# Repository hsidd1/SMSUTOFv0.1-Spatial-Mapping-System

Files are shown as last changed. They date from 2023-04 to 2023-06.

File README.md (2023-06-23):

# Spatial-Mapping-System
**The SMSUTOFv0.1 is an embedded spatial measurement device I've created which uses a VL53L1X time-of-flight sensor to acquire information about the area around you and generates a 3D mapping of a scanned area.**

Check out the datasheet for this project: [SMSUTOFv01 Datasheet](SMSUTOFv01-datasheet.pdf)

## Demo

<div style="display:flex; justify-content:center;">
  <div style="text-align:center;">
    <div>Area scanned:</div>
    
  </div>
  <div style="text-align:center;">
    <div>Output plot:</div>
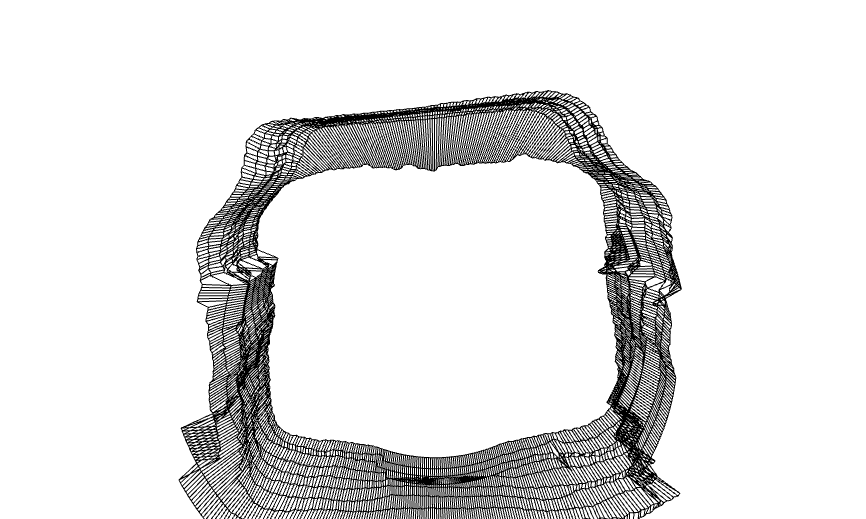
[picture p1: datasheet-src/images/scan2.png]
    
  </div>
</div>

## Setting up:

1. Build the circuit based on the following schematic:
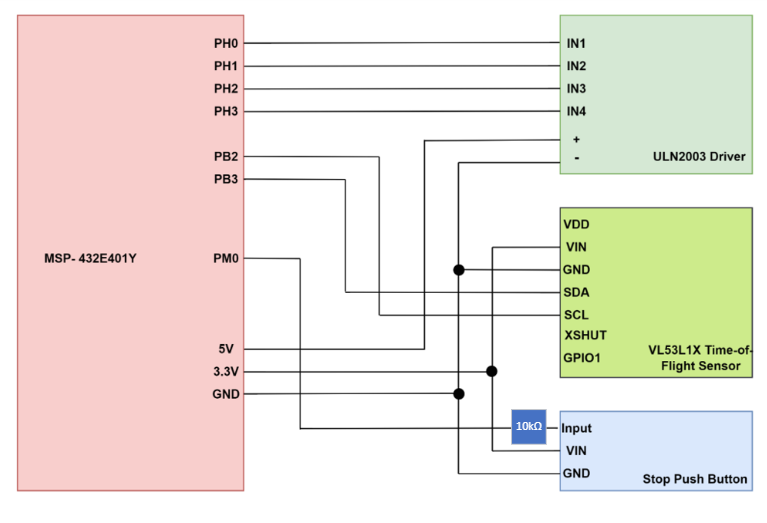
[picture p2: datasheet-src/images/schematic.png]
Circuit schematic


Ensure the ToF is mounted to the stepper motor. The Keil project should be flashed on the micro controller by default, so pressing the reset button is sufficient to load the program. If this is not the case: Open the Keil Project src found [here](main-keil) then translate, build and load the program.

## Software Installation:

The embedded C code can be run on [Keil uVision](https://www.keil.com/download/) and flashed directly onto the microcontroller from the IDE.

### Python Requirements

It is recommended to use a virtual environment, as this program uses libraries compatible upto [Python 3.9](https://www.python.org/downloads/). If you choose to do this with conda:

```sh
conda create -n <env-name> python=3.9
```

You can then install the required packages ([NumPy](https://numpy.org/doc/1.21/), [Open3D](http://www.open3d.org/docs/release/), and [Pyserial](https://pyserial.readthedocs.io/en/latest/pyserial.html)):

```sh
pip install -r requirements.txt
```

## How to use the device after setting up: 

1. Open `measurement_data.py` and modify the PORT variable to that of your device, found from UART port listed in device manager. 
2. Run `measurement_data.py` by opening terminal, navigating to the directory of the file, and entering `python measurement_data.py`
3. Enter how many displacement steps the scan will use when prompted by the program. 
4. Press the peripheral push button to enable measurements to set up the ToF. Pressing this again will toggle this back off.
5. Press the the onboard PJ1 button each time a measurement rotation has to be made. Pressing this again will end the rotation process.
6. For each number of physical steps taken, wait for the motor to complete one full rotation and return back to the home position. Once this is complete, move forward by the amount of x-displacement increment set (350 mm in the program but modifiable by user in the `STEP_INCREMENT` variable) 
7. Press the button again for the next measurement.
8. The program will then print to you the measurements at each point taken as the program runs from the scan and also output this to a file in the same directory called `pointdata.xyz`. D3 LED will flash on the micro controller for verification purposes. 
9. Run the `spatial_visualization.py` file by typing `python spatial_visualization.py` in terminal.
10. When prompted, enter the number of scans taken. The program will use this and then output the numerical value to the user in the console and output the visualization points on the screen in a GUI. Closing this screen will show a new screen with final spatial map in a GUI. 

The scan is of a yz-plane with x being the displacement taken for each scan. `y` and `z` are seen as the vertical plane that the motor rotates and scans for, and `x` is the displacement after physically moving the motor by the step increment defined.

The spatial map should now be visible to you in an interactive GUI window.

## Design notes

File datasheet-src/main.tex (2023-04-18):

\documentclass[12pt, letterpaper]{article}
\usepackage{graphicx}
\graphicspath{{images/}} 
\usepackage{titling}
\usepackage{amsmath}
\usepackage{listings}
\usepackage{xcolor}
\usepackage{textcomp}
\usepackage{multicol}
\usepackage[utf8]{inputenc}
\usepackage{parallel}
\usepackage{siunitx}
\usepackage{booktabs}
\usepackage{fancyhdr}
\usepackage{tabularx}
\usepackage{caption}
\usepackage[export]{adjustbox}
\usepackage[top=1in, left=0.5in, right=0.5in, bottom=1in]{geometry}
\addtolength{\topmargin}{0in}

\usepackage{libertine}
\renewcommand*\familydefault{\sfdefault}  %% Only if the base font of the document is to be sans serif
\usepackage[T1]{fontenc}

\title{Spatial Mapping System Using Time-of-Flight}
\author{Hamza Siddiqui - 400407170 - siddih38 }
\date{April 17, 2023}

%\begin{document}

\pagestyle{fancy}

\lhead{Hamza Siddiqui}
%\chead {\today}
\chead {April 17, 2023}
\rhead{SMSUTOF HS 2023 v0.1}

\onecolumn

\begin{figure}
\begin{minipage}{0.47\textwidth}
\centering
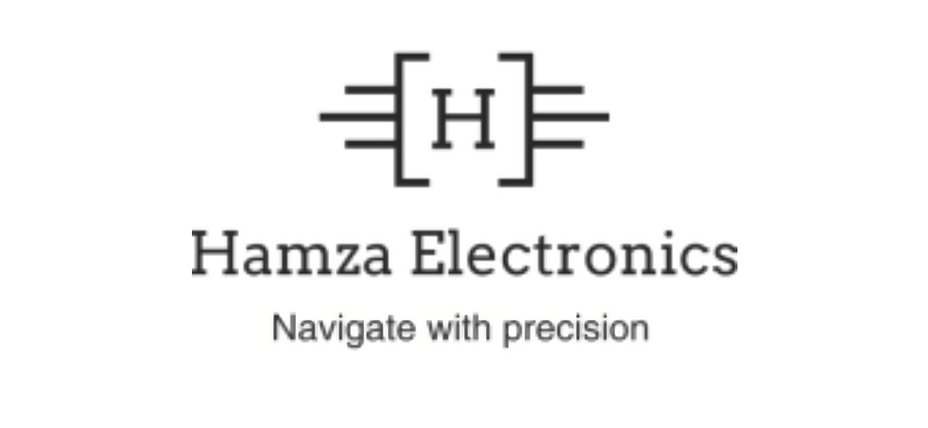
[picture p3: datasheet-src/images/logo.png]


\end{minipage}
\hfill
\begin{minipage}{0.47\textwidth}
\raggedleft
\Huge \textbf{Spatial Mapping System using ToF v0.1}
\end{minipage}
\end{figure}

\begin{figure}
\begin{minipage}{0.47\textwidth}

\section*{Core Device Components}
\begin{itemize}
    \item Microcontroller Unit (ARM\textregistered \ Cortex\textregistered-M4F TI MSP432E401Y SimpleLink\texttrademark) 
    \item Stepper Motor (28BYJ-48 Velleman\textregistered\ 5 VDC Stepper Motor with ULN2003 Driver Board)
    \item Time-of-Flight Sensor (ST FlightSense\texttrademark \ VL53L1X)
    \item Additional Push Button 
    \item Removable Sensor Mount (Hamza Electronics\texttrademark)
    \item Fiberboard Case (Hamza Electronics\texttrademark)
\end{itemize}

\end{minipage}
\hfill
\begin{minipage}{0.47\textwidth}
\centering
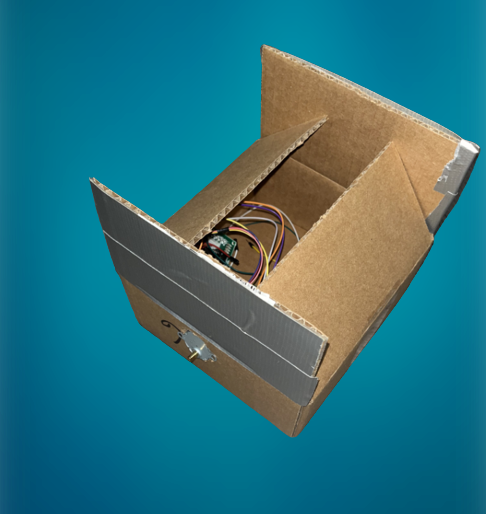
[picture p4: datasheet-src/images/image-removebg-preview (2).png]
 %PRODUCT IMAGE PLACEHOLDER

\end{minipage}
\end{figure}

\begin{document}
\maketitle
As a future member of the engineering profession, the student is responsible for performing the required work in an honest manner, without plagiarism and cheating.
Submitting this work with my name and student number is a statement and understanding that this work is my own and adheres to the Academic Integrity Policy of McMaster University and the Code of Conduct of the Professional Engineers of Ontario.
\thispagestyle{fancy}

\newpage
\section{Device Overview}
\subsection{Features}
\begin{multicols}{2}
\begin{itemize}
\item ARM Cortex-M4F TI MSP432E401Y Microcontroller (\$53.47)
    \begin{itemize}
        \item Bus frequency of 20MHz (configured via phase-locked loop; default core frequency of 120MHz)
        \item Four onboard LEDs - D3 flash functionality on each measurement
        \item Two onboard buttons (PJ1 for start/stop of motor rotation) and one reset button
        \item 1MB of flash, 256kB of SRAM
        \item  Communication interfaces including USB-OTG, CAN, Quad-SPI (QSSI), $\mathrm{I^2C}$, SPI,  and UART
        \item Two 12-Bit SAR-Based ADC Modules (2 Msps)
    \end{itemize}
\item MOT-28BYJ-48 Stepper Motor with ULN2003 driver (\$6.99)
    \begin{itemize}
        \item 5-12 VDC Operating Range 
        \item 64 steps/revolution 
        \item Frequency of 100Hz
        \item 4 phases with 4 step-indicator LEDs
    \end{itemize}
\item VL53L1X Time-of-Flight Sensor (\$25.32)
    \begin{itemize}
        \item Communication via $\mathrm{I^2C}$ (upto 400kHz)
        \item 4 m ranging and ranging frequency of 50Hz
        \item 2.6-5.5V supply range, 2.8V operating range
        \item Emitter: 940 nm invisible laser (Class1)
    \end{itemize}
\item Additional Push Button (\$0.60)
    \begin{itemize}
        \item Start/stop functionality for data acquisition
    \end{itemize}
\item Additional System Features
    \begin{itemize}
        \item UART serial communication between device and PC
        \item $\mathrm{I^2C}$ serial communication between device and Time-of-Flight sensor
        \item Baud rate of 115200
        \item C-language programming for device instructions, Python programming for visualization (via Pyserial and Open3d)
    \end{itemize}
\end{itemize}
\end{multicols}
\subsection{General Description}
To begin data acquisition, the additional push button is pressed to enable data processing, then the onboard button is pressed to begin taking measurements by spinning the motor and interfacing with the Time-of-Flight (ToF) sensor. The SMSUTOF HS 2023 utilizes a transducer which provides a digital output. Spatial distance measurements are acquired via the ToF sensor using $\mathrm{I^2C}$, while displacement is fixed at 30 cm. At each angle a measurement is taken, the D3 LED flashes. Together these measurements allow the device to measure a 3-D area. These signals are converted to electric signals, then conditioned into digital form and are finally converted to discrete digital values during the ADC process. The system communicates this to the user PC via UART asynchronous serial communication. A Python program is run on the PC and interfaces via their UART COM port and a baud rate of 115200, which then transfers measurement data to the PC and allows it to be stored in a .xyz file. This collected data is then used to generate a 3-D plot of the area that has been scanned via a Python program using open3d. The points for this plot are generated using trigonometric properties based on the angle and y,z coordinates generated, along with the fixed x-coordinate increment. If at anytime the button is pressed again during the scanning process, the data acquisition will be stopped. 
\subsection{Block Diagram (Data Flow Graph)}
\begin{figure}[h]
    \centering
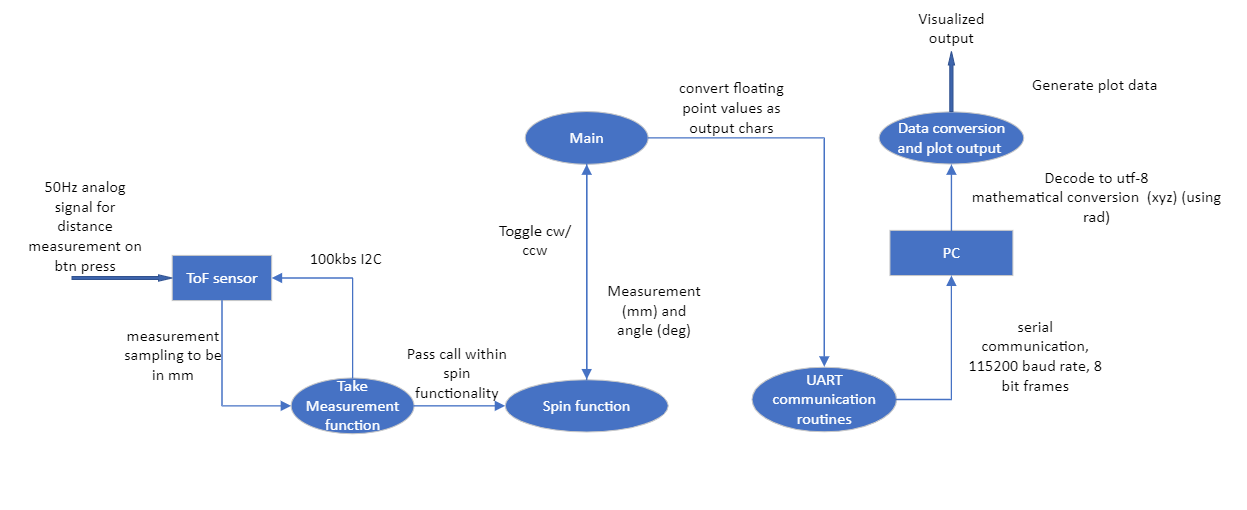
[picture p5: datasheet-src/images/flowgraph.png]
    
    \caption{Flow graph}
    \label{fig:flowgraph}
\end{figure}

\section{Device Characteristics Table}
\begin{center}
\begin{tabularx}{0.5\textwidth}{|>{\centering\arraybackslash}X|>{\centering\arraybackslash}X|>{\centering\arraybackslash}X|}
\hline
\textbf{Characteristic} & \textbf{Description} \\
\hline
Bus Speed & 20MHz \\
\hline
Serial Port & COM4 \\
\hline
Communication Speed & 115200 bps \\
\hline
Measurement Status & D3 \\
\hline
\end{tabularx}
\captionof{table}{Device Characteristics}
\end{center}

\begin{minipage}{0.48\textwidth}
\centering
\textbf{Stepper Motor Pin Assignments}
\begin{tabular}{|c|c|}
\hline
\textbf{ULN2003 Driver Board} & \textbf{MCU} \\
\hline
+ (5V) & 5V \\
\hline
- (5V) & GND \\
\hline
IN1 & PH0 \\
\hline
IN2 & PH1 \\
\hline
IN3 & PH2 \\
\hline
IN4 & PH3 \\
\hline
\end{tabular}
\captionof{table}{Stepper Motor Pinout}
\end{minipage}
\hfill
\begin{minipage}{0.48\textwidth}
\centering
\textbf{Time-of-Flight Sensor Pin Assignments}
\begin{tabular}{|c|c|}
\hline
\textbf{VL53L1X} & \textbf{MCU} \\
\hline
VDD & - \\
\hline
VIN & VCC (3.3V or 5V) \\
\hline
GND & GND \\
\hline
SDA & PB3 (I2C0 SDA) \\
\hline
SCL & PB2 (I2C0 SCL)  \\
\hline
XSHUT & - \\
\hline
GPIO1 & - \\
\hline
\end{tabular}
\captionof{table}{Time-of-Flight Sensor Pinout}
\end{minipage}

\section{Detailed Description}
\subsection{Distance Measurement}\label{Distance Measurement}
\textbf{Acquisition:}\\
The VL53L1X sensor utilizes Light Detection and Ranging (LIDAR) technology to accurately measure distances. It emits a pulse of light with a wavelength of 940 nm, which is then reflected back to the sensor by an object (maximum 4 m away). The sensor measures the time it takes for the emitted light pulse to reach the object and be reflected back to the detector. By utilizing the known speed of light and the measured time, the VL53L1X calculates the distance to the object with high accuracy as follows:
$$Measured\ Distance = \frac{Photon\ Travel\ Time}{2}\times Speed\ of\ Light$$ The sensor is mounted to a motor that completes 360 degree rotations (512 steps). At every 64 steps, or 45 degrees, a user LED is flashed to indicate a measurement (in mm) has been taken by the sensor. This is achieved through interfacing with the sensor and micro controller via $\mathrm{I^2C}$ serial communication. In total, this allows for 8 measurements to be taken in a single rotation, and the program can be modified to measure at smaller number of steps to take more measurements for more accuracy at the cost of time (use-case dependent configuration). \\ 
\textbf{Data Processing:} \\
Data is processed and converted via mathematical computation. When given the motor's angle $\theta$, the program increments by the measurement angle rotation each time and computes the coordinates using trigonometric properties. This is computed as $angle = steps/(TOTAL STEPS) \times 2\pi$ where steps is incremented by 45 degrees and TOTAL STEPS is set to 512 - these reset each time a rotation is complete i.e. when 512 steps have completed. For a given distance measurement $r$, we obtain that $y = r\cos{\theta}$ and $z = r\sin{\theta}$ for the vertical plane. X coordinate is computed through configuring a physical step increment taken for each successive measurement rotation in the program and incrementing the coordinate for the next spatial scan based on this value (350mm default configuration). This is the displacement for each scan. Together these coordinates can be used for plotting and mapping. \\
\textbf{Example Calculation:} 
\begin{figure}[h]
    \centering
    \begin{minipage}{0.5\textwidth}
        Suppose a measurement $r$ is measured as 3 m at an angle of 45 degrees. Then,
        \begin{align*}
            y &= r\cos{45}\\
              &= 3\cos{45}\\
              &= 2.12132034356 \ \text{m}
        \end{align*}
        and 
        \begin{align*}
            z &= r\sin{45}\\
              &= 3\sin{45}\\
              &= 2.12132034356 \ \text{m}
        \end{align*}
    \end{minipage}%
    \begin{minipage}{0.5\textwidth}
        \centering
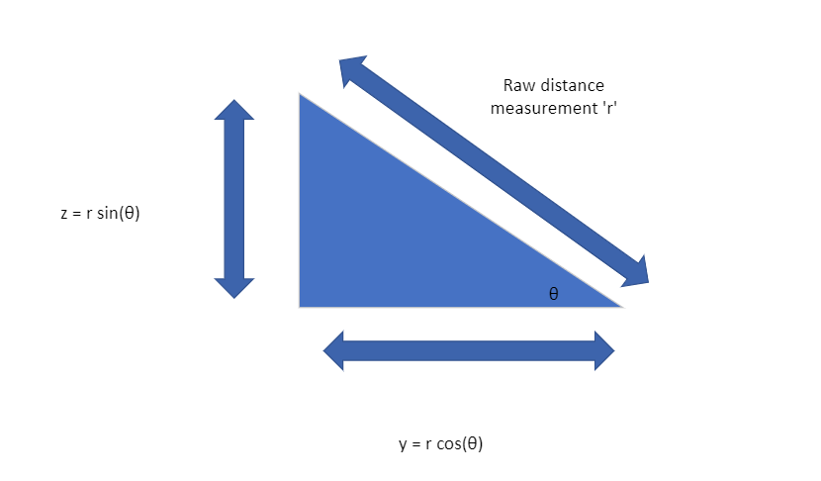
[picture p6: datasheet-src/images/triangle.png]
        
    \end{minipage}
    \caption{Trigonometric Conversion: Solving for $y$ and $z$ using the sine and cosine functions.}
    \label{fig:trig_conversion}
\end{figure}

\subsection{Visualization}
The visualization is achieved through Python using the NumPy, open3d, and PySerial libraries. Data is communicated using UART and a specified PORT which is accessed via PySerial. The measurement data from the micro controller is then communicated to the PC and is processed as points following the previously outlined conversion method. The points are then written to a .xyz file in the format of "x y z" per line, and is outputted on the console in the same manner for the user to view measurements printed in real time for each measurement. Next, using open3d, the points are viewed numerically by conversion using NumPy. 
\\Here is an example of how to read a point cloud using the Open3D library:

{\fontsize{10pt}{12pt}\selectfont % set font size to 10pt with 12pt line spacing
    \ttfamily % switch to monospaced font
    \begin{verbatim}
        pcd = o3d.io.read_point_cloud("pointdata.xyz", format="xyz")

    \end{verbatim}
}
In this code snippet, the variable \verb|pcd| stores the point cloud data read from the file \verb|pointdata.xyz|. The \verb|format| parameter specifies the format of the file, which in this case is XYZ format. 
These are then visualized using the following function call:
{\fontsize{10pt}{12pt}\selectfont % set font size to 10pt with 12pt line spacing
    \ttfamily % switch to monospaced font
    \begin{verbatim}
    o3d.visualization.draw_geometries([pcd])
    \end{verbatim}
}
Next, each vertex from the data is appended and the coordinates to connect lines in each yz slice is defined. The lines are then mapped to the 3D coordinate vertices as a line set and are then outputted to the GUI for visualization with the following function calls:
{\fontsize{10pt}{12pt}\selectfont % set font size to 10pt with 12pt line spacing
    \ttfamily % switch to monospaced font
    \begin{verbatim}
    line_set = o3d.geometry.LineSet(
        points=o3d.utility.Vector3dVector(np.asarray(pcd.points)),
        lines=o3d.utility.Vector2iVector(lines)
    )

    o3d.visualization.draw_geometries([line_set])
    \end{verbatim}
}

In this code snippet, the \verb|LineSet| class is used to create a line set from a set of points and lines. The \verb|points| argument is a vector of 3D points, and the \verb|lines| argument is a vector of pairs of point indices that define the line segments. The resulting line set is then visualized using the \verb|draw_geometries| function from the Open3D visualization module.

\section{Application Example with Expected Output}

A spatial scan can be taken of a room with a set number of displacement increments. An example room with an expected output can be seen below:

\begin{figure}[htbp]
\centering
\begin{minipage}{0.48\textwidth}
\centering

\subcaption{Hallway POV 1}
\label{fig:hallway1}
\end{minipage}
\hfill
\begin{minipage}{0.48\textwidth}
\centering

\subcaption{Hallway POV 2}
\label{fig:hallway2}
\end{minipage}
\caption{Hallway scanned}
\label{fig:hallways}
\end{figure}

\begin{figure}[htbp]
\centering
\fbox{\begin{minipage}{0.48\textwidth}
\centering
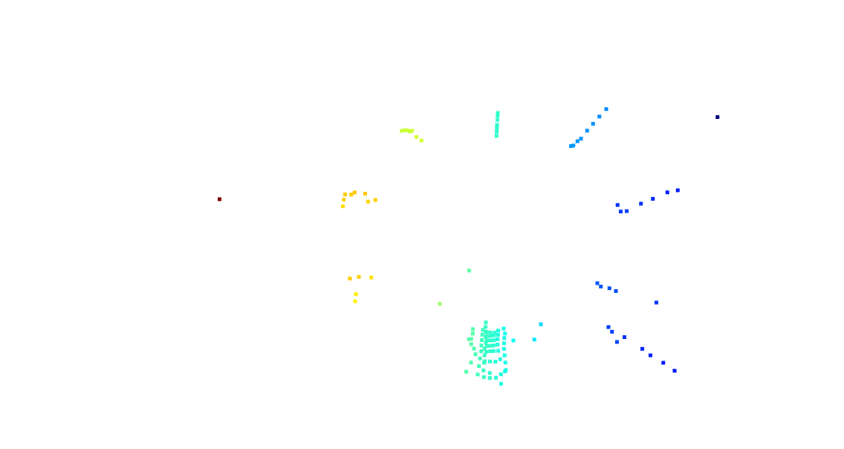
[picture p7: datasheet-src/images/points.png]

\subcaption{Point Visualization}
\label{fig:points}
\end{minipage}}
\hfill
\fbox{\begin{minipage}{0.48\textwidth}
\centering
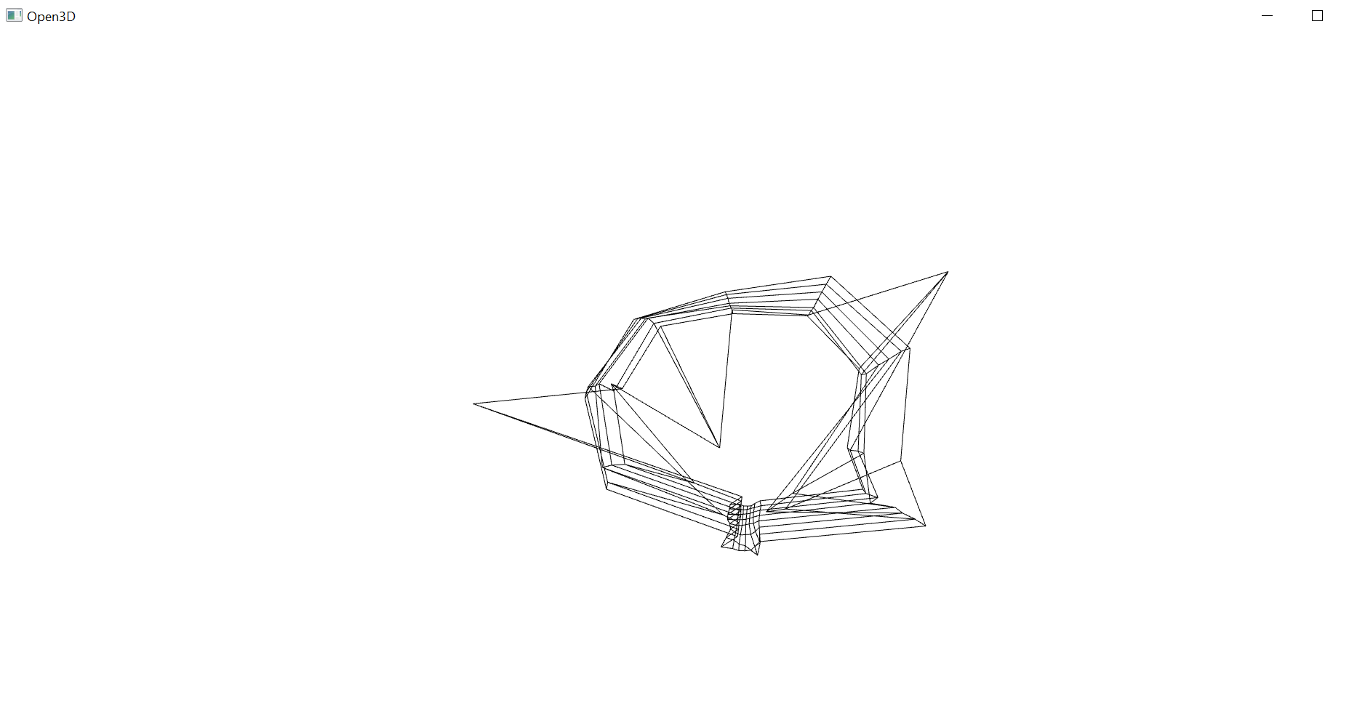
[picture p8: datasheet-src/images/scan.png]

\subcaption{Final output spatial map}
\label{fig:scan}
\end{minipage}}
\caption{Expected output of scan}
\label{fig:scan}
\end{figure}
 \newpage
\section{User's Guide}
Setting up: \\
Build the circuit based on the schematic provided in section \ref{sec:Circuit Schematic}. Ensure the ToF is mounted to the stepper motor. The Keil project should be flashed on the micro controller by default, so pressing the reset button is sufficient to load the program. If this is not the case: Open the Keil Project src from the provided code and $Translate$ \rightarrow build \rightarrow load. \\

Software Installation:
\begin{enumerate}
    \item Download Python 3.9, which can be found at https://www.python.org/downloads/ under specific release downloads.
    \item Install NumPy, open3d, and Pyserial by opening terminal and typing:
\begin{verbatim}
pip install numpy
pip install open3d
pip install pyserial
\end{verbatim}
Refer to their documentation for any issues:
\begin{itemize}
\item NumPy documentation: \url{https://numpy.org/doc/1.21/}
\item Open3D documentation: \url{http://www.open3d.org/docs/release/}
\item Pyserial documentation: \url{https://pyserial.readthedocs.io/en/latest/pyserial.html}
\end{itemize}
\end{enumerate}

How to use the device after setting up: 
\begin{enumerate}
    \item Open \verb|measurement_data.py| and modify the PORT variable to that of your device, found from UART port listed in device manager. 
    \item Run \verb|measurement_data.py| by opening terminal, navigating to the directory of the file, and entering \verb|python measurement_data.py|
    \item Enter how many displacement steps the scan will use when prompted by the program. 
    \item Press the peripheral push button to enable measurements to set up the ToF. Pressing this again will toggle this back off.
    \item Press the the onboard PJ1 button each time a measurement rotation has to be made. Pressing this again will end the rotation process.
    \item For each number of physical steps taken, wait for the motor to complete one full rotation and return back to the home position. Once this is complete, move forward by the amount of x-displacement increment set (350 mm in the program but modifiable by user in the \verb|STEP_INCREMENT| variable) 
    \item Press the button again for the next measurement.
    \item The program will then print to you the measurements at each point taken as the program runs from the scan and also output this to a file in the same directory called \verb|pointdata.xyz|. D3 LED will flash on the micro controller for verification purposes. 
    \item Run the \verb|spatial_visualization.py| file by typing \verb|python spatial_visualization.py| in terminal.
    \item When prompted, enter the number of scans taken. The program will use this and then output the numerical value to the user in the console and output the visualization points on the screen in a GUI. Closing this screen will show a new screen with final spatial map in a GUI. 
\end{enumerate}
As explained earlier, the scan is of a yz plane with x being the displacement taken for each scan. y and z are seen as the vertical plane that the motor rotates and scans for, and x is the displacement after physically moving the motor by the step increment defined. Refer to section \ref{Distance Measurement} for more detailed information with example calculations.

\section{Limitations}
\begin{itemize}
    \item \textbf{FLoating Point Capability: }The micro controllers features a 120-MHz Arm® Cortex®-M4F Processor Core With Floating Point Unit (FPU). The FPU fully supports various single-precision operations such as add, subtract, multiply, divide, multiply-and-accumulate, and square root. It also provides conversions between fixed-point and floating-point data formats, and floating-point constant instructions. It has 32 dedicated 32-bit single-precision registers, which are also addressable as 16 double-word registers. With the limitation of bits, the computations communicated to the PC are given with truncation. The trigonometric computations done by Python's math library add to this as the infinite series are accurate to limits of double-precision floating-point arithmetic, 15 to 17 decimal digits. Together the accumulation of these truncations result in an imperfect calculation of points, however minimal. Furthermore the trignometric functions assume fixed angle inputs, which may be subject to error by upto a few degrees, hence the point is not computed at the exact angle the sensor was oriented at. This allows for the points to still be accurate to a certain reasonable precision without being entirely perfect. 
    \item \textbf{ToF Quantization Error: } The ToF module includes a quantization error in the ADC process. Quantization error is the difference between the analog signal and the closest available digital value at each sampling instant from the A/D converter. It is equivalent to resolution. It is computed using $m = 8$ from  the ADC module bits and $V_{FS} = 3.3\ \text{V}$.
    \begin{align*}
        resolution &= \frac{V_{FS}}{2^m} \\
                   &= \frac{3.3}{2^8} \\
                   &= 0.0129\ \text{V}
    \end{align*}
    \item \textbf{Serial Communication: } The maximum serial communication rate of the PC can be found from device manager and is seen as 128000 bps as seen in the UART port. The rate is limited when using the micro controller as the rate is capped at a baud rate of 115200 bps. This can be verified by interfacing with UART at different baud rates until receiving an error. An example can be seen below: 

\begin{figure}[htbp]
\centering
\begin{minipage}{0.48\textwidth}
\centering
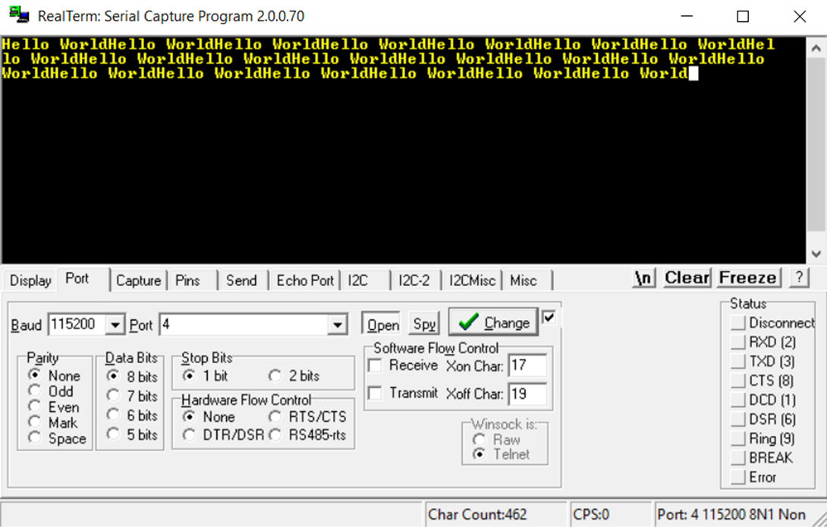
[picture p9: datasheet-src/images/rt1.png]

\subcaption{RealTerm output at 115200 baud rate}
\label{fig:rt1}
\end{minipage}
\hfill
\begin{minipage}{0.48\textwidth}
\centering
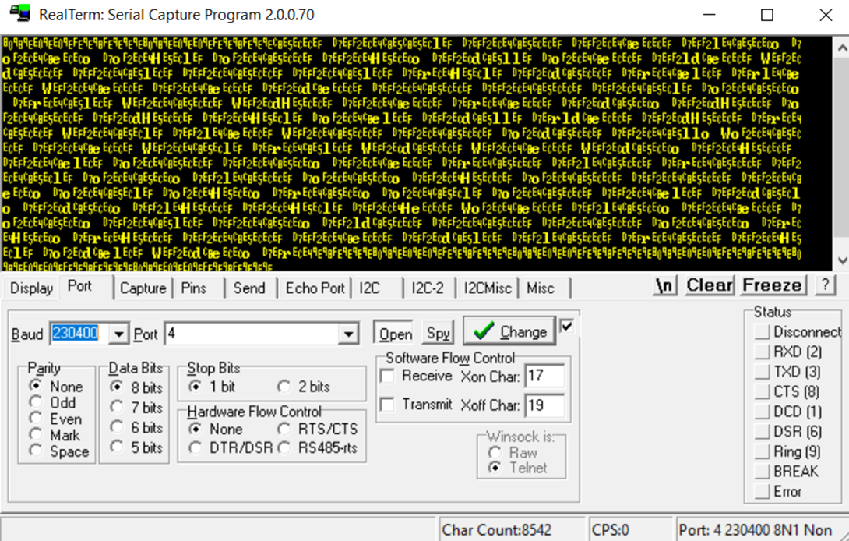
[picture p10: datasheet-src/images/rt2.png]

\subcaption{RealTerm output above 115200 bps}
\label{fig:rt2}
\end{minipage}
\caption{Verification of maximum standard serial communication rate}
\label{fig:rt_verification}
\end{figure}
The microcontroller and time-of-flight modules communicate via I2C serial communication. The I2C ports on the microcontroller are configured with a 100 kbps clock (in standard mode), as specified in the datasheet. In this setup, the microcontroller assumes the role of leader while the time-of-flight sensor acts as the follower and operates based on the microcontroller's clock speed. 

\item \textbf{Speed Limitations: } The speed of the stepper motor is accounted for with 512 steps and delays using \verb|SystickWait(4000)| with a 20MHz bus speed. This gives a motor speed of 0.4096 s per rotation without measurement delays between. 
The ToF also had a speed limitation with a very quick default speed from the overall calculation formula mentioned, however the delays within the program outweigh this speed and become the limitation. The delay called was of 50ms. This was verified by toggling a GPIO output port before and after spinning, and before and after measuring, then visualizing this using oscilloscope probes from an Analog Discovery 2 board with a generated waveform, and visualizing the pulse generated for each. 
\end{itemize} 
\\
\section{Circuit Schematic}\label{sec:Circuit Schematic}

Below is the circuit schematic for the device:

\begin{figure}[htbp]
\centering

\caption{Circuit Schematic}
\end{figure}
\newpage
\section{Programming Logic Flowchart(s)}
Below is the programming logic flowchart of the system:
\begin{figure}[htbp]
\centering
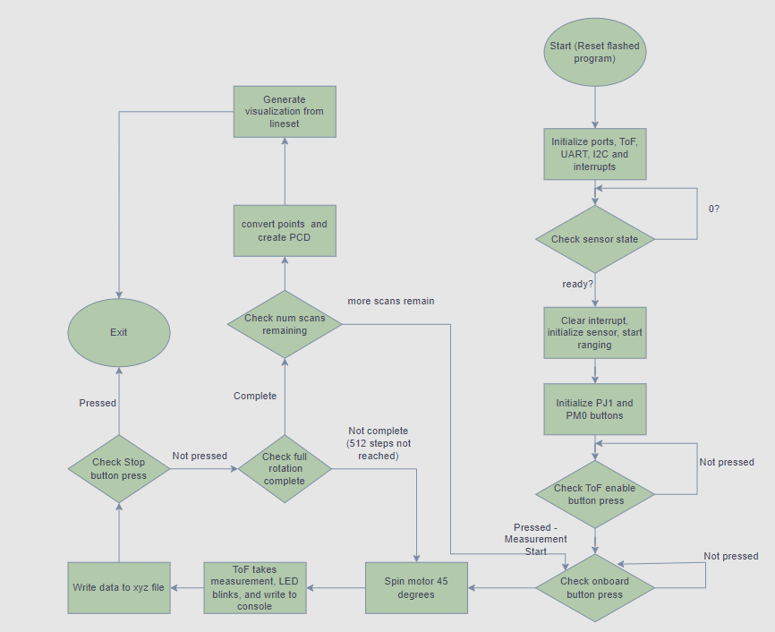
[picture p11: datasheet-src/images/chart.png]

\caption{Logic Flowchart}
\end{figure}
\newpage
\section{Additional Diagrams}
\begin{figure}[htbp]
\centering
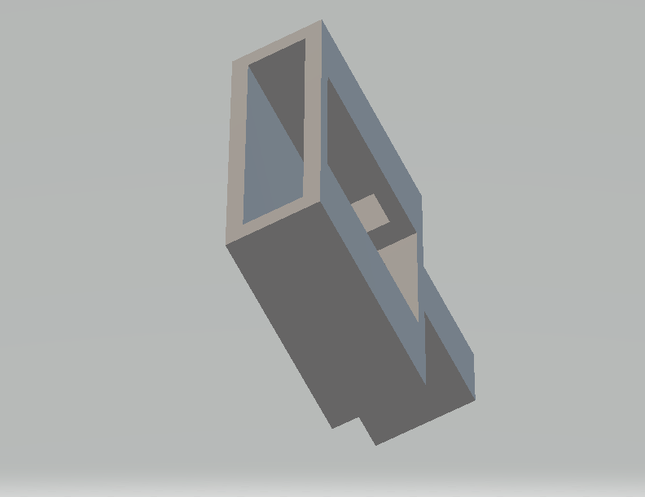
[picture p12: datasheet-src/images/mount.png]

\caption{ToF Mount STL}
\end{figure}
\end{document}

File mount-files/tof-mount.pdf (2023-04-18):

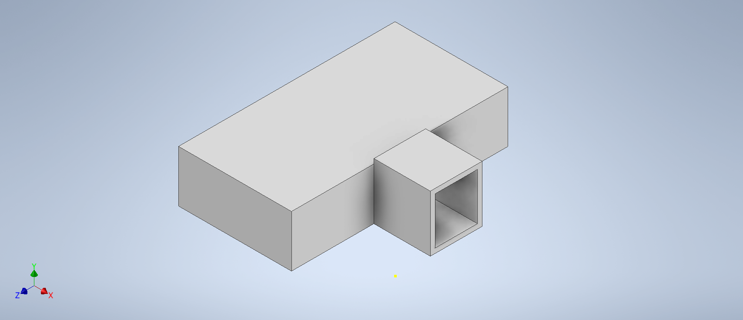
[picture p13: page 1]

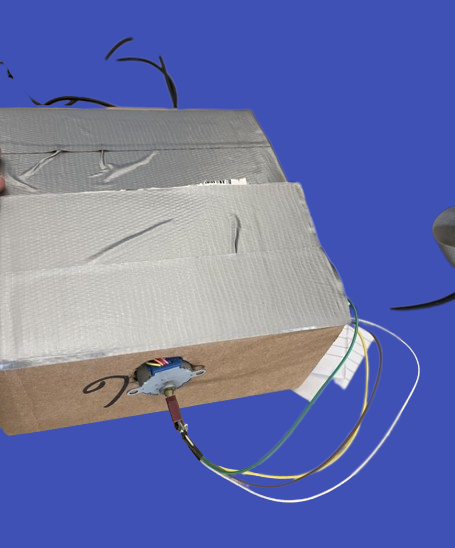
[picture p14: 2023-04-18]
datasheet-src/images/product.png

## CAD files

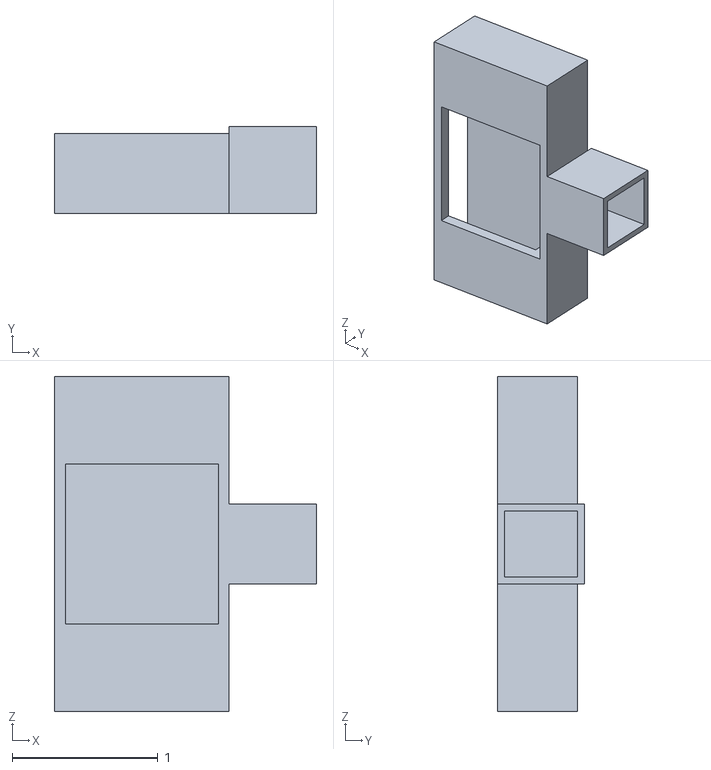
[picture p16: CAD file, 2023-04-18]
mount-files/tof-mount.stl
1.80 x 0.6 x 2.30

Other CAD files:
mount-files/tof-mount.ipt

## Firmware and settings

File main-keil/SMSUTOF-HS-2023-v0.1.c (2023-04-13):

#include <stdint.h>
#include "PLL.h"
#include "SysTick.h"
#include "uart.h"
#include "onboardLEDs.h"
#include "tm4c1294ncpdt.h"
#include "VL53L1X_api.h"
//#include "math.h"

// I2C configuration        
#define I2C_MCS_ACK             0x00000008  // Data Acknowledge Enable
#define I2C_MCS_DATACK          0x00000008  // Acknowledge Data
#define I2C_MCS_ADRACK          0x00000004  // Acknowledge Address
#define I2C_MCS_STOP            0x00000004  // Generate STOP
#define I2C_MCS_START           0x00000002  // Generate START
#define I2C_MCS_ERROR           0x00000002  // Error
#define I2C_MCS_RUN             0x00000001  // I2C Master Enable
#define I2C_MCS_BUSY            0x00000001  // I2C Busy
#define I2C_MCR_MFE             0x00000010  // I2C Master Function Enable

#define MAXRETRIES              5           // number of receive attempts before giving up

// initialising ports, protocols, etc
void I2C_Init(void){
  SYSCTL_RCGCI2C_R |= SYSCTL_RCGCI2C_R0;           													// activate I2C0
  SYSCTL_RCGCGPIO_R |= SYSCTL_RCGCGPIO_R1;          												// activate port B
  while((SYSCTL_PRGPIO_R&0x0002) == 0){};																		// ready?
    GPIO_PORTB_AFSEL_R |= 0x0C;           																	// 3) enable alt funct on PB2,3       0b00001100
    GPIO_PORTB_ODR_R |= 0x08;             																	// 4) enable open drain on PB3 only
    GPIO_PORTB_DEN_R |= 0x0C;             																	// 5) enable digital I/O on PB2,3
//    GPIO_PORTB_AMSEL_R &= ~0x0C;          																// 7) disable analog functionality on PB2,3
                                                                            // 6) configure PB2,3 as I2C
//  GPIO_PORTB_PCTL_R = (GPIO_PORTB_PCTL_R&0xFFFF00FF)+0x00003300;
  GPIO_PORTB_PCTL_R = (GPIO_PORTB_PCTL_R&0xFFFF00FF)+0x00002200;    //TED
    I2C0_MCR_R = I2C_MCR_MFE;                      													// 9) master function enable
    I2C0_MTPR_R = 0b0000000000000101000000000111011;                       	// 8) configure for 100 kbps clock (added 8 clocks of glitch suppression ~50ns)
//    I2C0_MTPR_R = 0x3B;                                        						// 8) configure for 100 kbps clock
}

//The VL53L1X needs to be reset using XSHUT.  We will use PG0
void PortG_Init(void){
    //Use PortG0
    SYSCTL_RCGCGPIO_R |= SYSCTL_RCGCGPIO_R6;                // activate clock for Port N
    while((SYSCTL_PRGPIO_R&SYSCTL_PRGPIO_R6) == 0){};    // allow time for clock to stabilize
    GPIO_PORTG_DIR_R &= 0x00;                                        // make PG0 in (HiZ)
  GPIO_PORTG_AFSEL_R &= ~0x01;                                     // disable alt funct on PG0
  GPIO_PORTG_DEN_R |= 0x01;                                        // enable digital I/O on PG0
                                                                                                    // configure PG0 as GPIO
  //GPIO_PORTN_PCTL_R = (GPIO_PORTN_PCTL_R&0xFFFFFF00)+0x00000000;
  GPIO_PORTG_AMSEL_R &= ~0x01;                                     // disable analog functionality on PN0

    return;
}

//XSHUT     This pin is an active-low shutdown input; 
//					the board pulls it up to VDD to enable the sensor by default. 
//					Driving this pin low puts the sensor into hardware standby. This input is not level-shifted.
void VL53L1X_XSHUT(void){
    GPIO_PORTG_DIR_R |= 0x01;                                        // make PG0 out
    GPIO_PORTG_DATA_R &= 0b11111110;                                 //PG0 = 0
    FlashAllLEDs();
    SysTick_Wait10ms(10);
    GPIO_PORTG_DIR_R &= ~0x01;                                            // make PG0 input (HiZ)
    
}

// Initializing port H for stepper motor 
void PortH_Init(void){
    //Use PortM pins for output
    SYSCTL_RCGCGPIO_R |= SYSCTL_RCGCGPIO_R7;                // activate clock for Port N
    while((SYSCTL_PRGPIO_R&SYSCTL_PRGPIO_R7) == 0){};   // allow time for clock to stabilize
    GPIO_PORTH_DIR_R |= 0xFF;                                       // make PN0 out (PN0 built-in LED1)
  GPIO_PORTH_AFSEL_R &= ~0xFF;                                  // disable alt funct on PN0
  GPIO_PORTH_DEN_R |= 0xFF;                                     // enable digital I/O on PN0
                                                                                                    // configure PN1 as GPIO
  //GPIO_PORTM_PCTL_R = (GPIO_PORTM_PCTL_R&0xFFFFFF0F)+0x00000000;
  GPIO_PORTH_AMSEL_R &= ~0xFF;                                  // disable analog functionality on PN0      
    return;
}

// Initialising for configuring ports for onboard assigned LED
void PortF0F4_Init(void) { // F4 - measurement status, F0 - Additional status
    SYSCTL_RCGCGPIO_R |= SYSCTL_RCGCGPIO_R5; //activate the clock for Port F
    while ((SYSCTL_PRGPIO_R & SYSCTL_PRGPIO_R5) == 0) {};//allow time for clock to stabilize
    GPIO_PORTF_DIR_R = 0b00010001; //Make PF0 and PF4 outputs, to turn on LED's
    GPIO_PORTF_DEN_R = 0b00010001;
    return;
}

// Initiasiling Port M for buttons - start/stop spinning and start/stop recording
void PortM0M1M2M3_Init(void) {
    SYSCTL_RCGCGPIO_R |= SYSCTL_RCGCGPIO_R11; //activate the clock for Port M
    while ((SYSCTL_PRGPIO_R & SYSCTL_PRGPIO_R11) == 0) {}; //allow time for clock to stabilize
    GPIO_PORTM_DIR_R = 0b00000000; // Make PM0:PM3 inputs, reading if the button is pressed or not
    GPIO_PORTM_DEN_R = 0b00001111; // Enable PM0:PM3
    return;
}

// Give clock to Port J and initalize as input GPIO-- 0 and 1 for now 
void PortJ_Init(void){
	SYSCTL_RCGCGPIO_R |= SYSCTL_RCGCGPIO_R8;					// Activate clock for Port J
	while((SYSCTL_PRGPIO_R&SYSCTL_PRGPIO_R8) == 0){};	// Allow time for clock to stabilize
  GPIO_PORTJ_DIR_R &= ~0x03;    										// Make PJ1 input 
  GPIO_PORTJ_DEN_R |= 0x03;     										// Enable digital I/O on PJ1
	
	GPIO_PORTJ_PCTL_R &= ~0x000000FF;	 								//? Configure PJ1 as GPIO 
	GPIO_PORTJ_AMSEL_R &= ~0x03;											//??Disable analog functionality on PJ1		
	GPIO_PORTJ_PUR_R |= 0x03;													//	Enable weak pull up resistor
}
// Interrupt initialization for GPIO Port J IRQ# 51
void PortJ_Interrupt_Init(void){
	
		FallingEdges = 0;       // initialize counter

	
		GPIO_PORTJ_IS_R = 0;    	// (Step 1) PJ1 is edge-sensitive 
		GPIO_PORTJ_IBE_R = 0;   	//     			PJ1 is not both edges 
		GPIO_PORTJ_IEV_R = 0;    	//     			PJ1 falling edge event 
		GPIO_PORTJ_ICR_R = 0x02;     // 					clear interrupt flag by setting proper bit in ICR register
		GPIO_PORTJ_IM_R = 0x02;    	// 					arm interrupt on PJ1 by setting proper bit in IM register
    
		NVIC_EN1_R = 0x00080000;           // (Step 2) enable interrupt 51 in NVIC
	
		NVIC_PRI12_R = 0xA0000000; 				// (Step 4) set interrupt priority 5

		EnableInt();           							// (Step 3) Enable Global Interrupt. lets go!
}
//	(Step 5) IRQ Handler (Interrupt Service Routine).  
//  				This must be included and match interrupt naming convention
//	 				in startup_msp432e401y_uvision.s 
//					(Note - not the same as Valvano textbook).
void GPIOJ_IRQHandler(void){
  FallingEdges = FallingEdges + 1;	// Increase the global counter variable ;Observe in Debug Watch Window
	GPIO_PORTJ_ICR_R = 0x02;     					// acknowledge flag by setting proper bit in ICR register
  if ((GPIO_PORTJ_DATA_R & 0b00000010) == 0){
 SysTick_Wait10ms(10);
				return;
             }
      if ((GPIO_PORTJ_DATA_R & 0b00000001) == 0){
while(sensorState==0){
			status = VL53L1X_BootState(dev, &sensorState);
			SysTick_Wait10ms(10);
      FlashLED2();
		}
          }
										//Flash the LED D2 one time
													//Flash the LED D2 one time
	GPIO_PORTJ_ICR_R = 0x03;     					// Acknowledge flag by setting proper bit in ICR register
}

// init function calls
void FlashLED(int flash_count);
void spin_cw(uint8_t dataReady, uint16_t Distance);
void spin_ccw(uint8_t dataReady, uint16_t Distance);
void take_measurement(uint8_t dataReady, uint16_t Distance);
void bus_pulse();
/* *********************************************************************************************/
// ******************************* !! MAIN CODE BEGINS !! *********************************** //
/* ********************************************************************************************/

/*
This program interfaces with a Time of Flight sensor using I2C and takes measurements after rotating the sensor on a motor.
The motor is programmed to spin clockwise then return home. 
An onboard button PJ1 sets an interrupt routine in the program to allow for measurements to be taken.
Run this after running the respective python file to allow for measurements to be recorded.
*/ 

uint16_t	dev = 0x29;			//address of the ToF sensor as an I2C slave peripheral
int status=0;
int totalsteps = 0;
// flags for measure and spin button toggle
int startstop_measure = 0;
int startstop_spin = 0;

// call for bus speed measurement 
void bus_pulse(){
  while(1){
		GPIO_PORTN_DATA_R=0b00001111;
		SysTick_Wait(20000);
		GPIO_PORTN_DATA_R=0b00000000;
		SysTick_Wait(20000);
	}
}

// Flashes D3 - takes parameter for number of flashes
void FlashLED(int flash_count){
    for (int i = 0; i < flash_count; i++) {
    GPIO_PORTF_DATA_R ^= 0b10000; // F4
    SysTick_Wait10ms(1);
    GPIO_PORTF_DATA_R ^= 0b10000;
    SysTick_Wait10ms(1);
    }
}

// spinning clockwise and measuring
void spin_cw(uint8_t dataReady, uint16_t Distance){
    int delay = 4000; // minimum delay between states for given clock
    int angle = 64; // 512/8 = 64
    int measure_point = 16; // 64/4 = 16 
		for (int j = 0; j < angle; j++){ 
      // 64 steps --> 45 deg (360 / 8): 4 state changes 45/4 = 11.25 deg
		  GPIO_PORTH_DATA_R = 0b00001001;
      SysTick_Wait(delay);
      GPIO_PORTH_DATA_R = 0b00000011;
      SysTick_Wait(delay);
      GPIO_PORTH_DATA_R = 0b00000110;
      SysTick_Wait(delay);
      GPIO_PORTH_DATA_R = 0b00001100;
      SysTick_Wait(delay);
      totalsteps++;
		}
    // stop button
    if((GPIO_PORTJ_DATA_R & 0b00000001) == 0){
      SysTick_Wait10ms(10);
				return;
    }
		if(totalsteps % measure_point == 0){ // 16 (64/4) increments is 11.25 deg (45/4)
      FlashLED(3);
      take_measurement(dataReady, Distance);
		}     
}

// spinning counter clockwise and measuring 
void spin_ccw(uint8_t dataReady, uint16_t Distance){
    int delay = 4000; // minimum delay between states for given clock
    int angle = 64; // 512/8 = 64
    int measure_point = 16; // 64/4 = 16 
		for (int j = 0; j < angle; j++){ 
      // 64 steps --> 45 deg (360 / 8): 4 state changes 45/4 = 11.25 deg
      GPIO_PORTH_DATA_R = 0b00001100;		
      SysTick_Wait(delay);
			GPIO_PORTH_DATA_R = 0b00000110;
      SysTick_Wait(delay);
			GPIO_PORTH_DATA_R = 0b00000011;
      SysTick_Wait(delay);
			GPIO_PORTH_DATA_R = 0b00001001;
      SysTick_Wait(delay);
      totalsteps++;
		}
    // stop button PJ1 
    if((GPIO_PORTJ_DATA_R & 0b00000001) == 0){
      SysTick_Wait10ms(10);
				return;
    }
		if(totalsteps % measure_point == 0){ // 16 (64/4) increments is 11.25 deg (45/4)
      FlashLED(3);
      take_measurement(dataReady, Distance);
		}     
}

void take_measurement(uint8_t dataReady, uint16_t Distance){
  
  //wait until the ToF sensor's data is ready
  while (dataReady == 0){
    status = VL53L1X_CheckForDataReady(dev, &dataReady);
    FlashLED3(1);
    VL53L1_WaitMs(dev, 5);
  }
  dataReady = 0;

  // store received data
  status = VL53L1X_GetDistance(dev, &Distance);					//The Measured Distance value
  status = VL53L1X_ClearInterrupt(dev); /* clear interrupt has to be called to enable next interrupt*/
  // Print the resulted readings to UART
  sprintf(printf_buffer,"%u\n",Distance);
  UART_printf(printf_buffer);
  SysTick_Wait10ms(50);
  }

int main(void) {
  // varaibles to store tof data 
  uint8_t byteData, sensorState=0, myByteArray[10] = {0xFF, 0xFF, 0xFF, 0xFF, 0xFF, 0xFF, 0xFF, 0xFF, 0xFF, 0xFF} , i=0;
  uint16_t wordData;
  uint16_t Distance;
  uint16_t SignalRate;
  uint16_t AmbientRate;
  uint16_t SpadNum; 
  uint8_t RangeStatus;
  uint8_t dataReady;

	//initialisation 
	PLL_Init();	
	SysTick_Init();
	onboardLEDs_Init();
	I2C_Init();
	UART_Init();
	
  // init ports
  PortM0M1M2M3_Init();
  PortF0F4_Init();
  PortH_Init();
  PortJ_Init();
	PortJ_Interrupt_Init();	


  // 	status = VL53L1X_GetSensorId(dev, &wordData);
  // 	sprintf(printf_buffer,"(Model_ID, Module_Type)=0x%x\r\n",wordData);
  // 	UART_printf(printf_buffer);


  // uncomment and connect probes to ad2 to check bus speed of system 
  //bus_pulse();
  // Booting ToF chip

  // getting sensor state 
  while(sensorState==0){
  status = VL53L1X_BootState(dev, &sensorState);
  SysTick_Wait10ms(10);
  }
  //FlashAllLEDs();
  //UART_printf("ToF Chip Booted!\r\n Please Wait...\r\n");

  status = VL53L1X_ClearInterrupt(dev); /* clear interrupt has to be called to enable next interrupt*/

  /* Initialize sensor in default mode - ranges at 10 Hz in Long distance mode */
  status = VL53L1X_SensorInit(dev);
  Status_Check("SensorInit", status);

    
  /* Optional functions to be used to change the main ranging parameters according the application requirements to get the best ranging performances */
  //  status = VL53L1X_SetDistanceMode(dev, 2); /* 1=short, 2=long */
  //  status = VL53L1X_SetTimingBudgetInMs(dev, 100); /* in ms possible values [20, 50, 100, 200, 500] */
  //  status = VL53L1X_SetInterMeasurementInMs(dev, 200); /* in ms, IM must be > = TB */

  status = VL53L1X_StartRanging(dev);   // This function has to be called to enable the ranging

  // main loop - ranging enabled and ready to measure 
	while(1){
		//wait for interupt from button to start
		WaitForInt();
		// Booting ToF chip
		while(sensorState==0){
			status = VL53L1X_BootState(dev, &sensorState);
			SysTick_Wait10ms(10);
		}

		status = VL53L1X_ClearInterrupt(dev); 
		
		/* This function must to be called to initialize the sensor with the default setting  */
		status = VL53L1X_SensorInit(dev);
		Status_Check("SensorInit", status);
		status = VL53L1X_StartRanging(dev);   // This function has to be called to enable the ranging

  
  for(int i = 0; i < 8; i++) { // 64*8 = 512
    // Wait until the ToF sensor's data is ready
    while (dataReady == 0){
        status = VL53L1X_CheckForDataReady(dev, &dataReady);
        VL53L1_WaitMs(dev, 5);
    }
    dataReady = 0;
    
    // Read the data values from ToF sensor
    status = VL53L1X_GetRangeStatus(dev, &RangeStatus);
    status = VL53L1X_GetDistance(dev, &Distance); // The Measured Distance value
    status = VL53L1X_GetSignalRate(dev, &SignalRate);
    status = VL53L1X_GetAmbientRate(dev, &AmbientRate);
    status = VL53L1X_GetSpadNb(dev, &SpadNum);
    
    status = VL53L1X_ClearInterrupt(dev); /* clear interrupt has to be called to enable next interrupt*/
    
    // Print the resulted readings to UART
    sprintf(printf_buffer,"%u\r\n", Distance);
    UART_printf(printf_buffer);
    
    // Flash LED and delay before next measurement
    GPIO_PORTF_DATA_R = 0b00000001;
    SysTick_Wait10ms(30);
    GPIO_PORTF_DATA_R = 0b00000000;
    spin_cw();
    SysTick_Wait10ms(150);
}
// Spin motor in opposite direction to complete a full rotation
spin_ccw();
// Stop ranging after taking all measurements
VL53L1X_StopRanging(dev);

// removing temporarily
int temp = 0
if(temp){ 
// Loop through 8 times to spin the motor in opposite directions to take additional measurements
for(int i = 0; i < 8; i++) { // 360 / 32 = 11.25
    int dir = 0;
    if(!dir){
        // Check for peripheral button press to stop
        if((GPIO_PORTM_DATA_R&0b00000001)==0){
            SysTick_Wait10ms(10);
            break;
        }
        // Spin motor clockwise and take distance measurements
        spin_cw(dataReady, Distance);	
        totalsteps = 0;
    }else if (dir){
        // Check for peripheral button press to stop
        if((GPIO_PORTM_DATA_R&0b00000001)==0){
            SysTick_Wait10ms(10);
            break;
        }
        // Spin motor counterclockwise and take distance measurements
        spin_ccw(dataReady, Distance); 
        totalsteps = 0;
    }
    // toggle to switch direction again
    dir ^= 1;

    // Stop ranging after taking all measurements
    VL53L1X_StopRanging(dev);
    // Wait indefinitely
   // while(1) {}
  }
}

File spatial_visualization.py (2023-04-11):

#
#   Modified by Hamza Siddiqui - 400407170 - siddih38

#   Purpose: This example Python program simulates data received from a
#   sensor by writing the expected format of example data to a file. The
#   visualization will be demonstrated using a Python module called Open3D.
#
#   Special notes:
#       1. Open3D only works with Pythons 3.6-3.9.  It does not work with 3.10
#       2. For this eample you should run it in IDLE.  Anaconda/Conda/Jupyter
#       require different Open3D graphing methods (these methods are poorly documented)
#       3. Under Windows 10 you may need to install the MS Visual C++ Redistributable bundle
#           https://docs.microsoft.com/en-us/cpp/windows/latest-supported-vc-redist?view=msvc-170
#       4. VirtualBox does not support OpenGL. If you're running Windows under Virtualbox or
#       your system doesn't support OpenGL (very rare), then you can install an OpenGL emulator dll
#           https://fdossena.com/?p=mesa/index.frag (unzip and copy opengl32.dll into Python dir)
#
#   T. Doyle
#   March 18, 2022 (Updated 2020 example)
#

'''
Run this program after acquiring measurement data into file from measurement_data.py. This program reads data from the file
and  outputs a 3D spatial mapping from the measurements obtained

'''
# Importing necessary libraries
import numpy as np
import open3d as o3d

if __name__ == "__main__":
    num_scans = int(input("Enter how many scans taken:"))
    # Set number of rotations
    ROTATIONS = 16

    #Read the test data in from the file we created        
    print("Read in the prism point cloud data (pcd)")
    pcd = o3d.io.read_point_cloud("pointdata.xyz", format="xyz")

    #Lets see what our point cloud data looks like numerically       
    print("The PCD array:")
    print(np.asarray(pcd.points))
    #Lets see what our point cloud data looks like graphically       
    print("Lets visualize the PCD: (spawns seperate interactive window)")
    o3d.visualization.draw_geometries([pcd])
    
    # append each vertex from data
    yz_slice_vertex = [i for i in range(0,num_scans*ROTATIONS)]
  

    #Define coordinates to connect lines in each yz slice        
    lines = []  
    for x in range(0,num_scans*ROTATIONS,ROTATIONS):
        for i in range(ROTATIONS):
            if i==ROTATIONS-1:
                lines.append([yz_slice_vertex[x+i], yz_slice_vertex[x]])
            else:
                lines.append([yz_slice_vertex[x+i], yz_slice_vertex[x+i+1]])
    
    #Define coordinates to connect lines between current and next yz slice        
    for x in range(0,num_scans*ROTATIONS-ROTATIONS-1,ROTATIONS):
        for i in range(ROTATIONS):
            lines.append([yz_slice_vertex[x+i], yz_slice_vertex[x+i+ROTATIONS]])

    #This line maps the lines to the 3d coordinate vertices
    line_set = o3d.geometry.LineSet(points=o3d.utility.Vector3dVector(np.asarray(pcd.points)),lines=o3d.utility.Vector2iVector(lines))

    #Lets see what our point cloud data with lines looks like graphically       
    o3d.visualization.draw_geometries([line_set]) # Opens GUI of visualization
                                    
    
 

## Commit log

2023-04-09 done with some errors
    [SMSUTOF-HS-2023-v0.1.c]
2023-04-12 update button press
2023-04-18 finalized datasheet of device
2023-04-18 Added 3D printed Inventor files for TOF mount mounted to stepper motor.
    These files contain designs for a TOF mount used for mounting a Time-of-Flight (TOF) sensor on a stepper motor for use on a robot or other device. The design was created in Autodesk Inventor and can 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
    [tof-mount.ipt, tof-mount.stl]
